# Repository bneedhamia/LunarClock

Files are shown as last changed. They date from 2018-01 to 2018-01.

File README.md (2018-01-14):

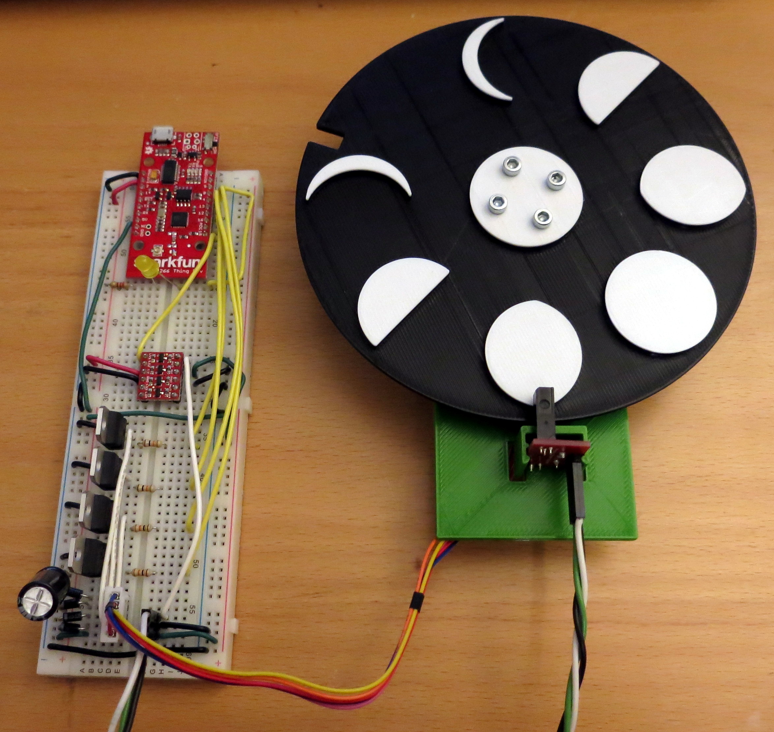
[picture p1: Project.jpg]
The Project so far

# LunarClock
An ESP8266 Thing Arduino Sketch to display the current phase of the moon,
as reported by
[HM Nautical Almanac Office: Miscellanea, Daily Rise/set and Twilight times for the British Isles](http://astro.ukho.gov.uk/nao/miscellanea/birs2.html). It does this by rotating a disk
that has 8 lunar images on it, to align the appropriate image with a window in the clock.

That page provides the time of sunrise/sunset/etc., for many locations in Britain and Ireland.
The end of that page provides the age of the moon (days since the new moon) and
the percentage of its face that is illuminated. Of all that information, only the age of the moon
is used by this Sketch.

The current Sketch requires a Sparkfun EPS8266 Thing Dev board, a Photo-interrupter,
and an AdaFruit 28BYJ-48 12V stepper motor, among other things.
Details are in the .ino Sketch PIN_ definitions and in BillOfMaterials.ods.

NOTE: This is a work in progress.

State of the project: On reset, the Sketch turns the lunar disk wheel to find the slot, then turns it to align
the first lunar image in the (to be built) clock window. It then connects to the local WiFi,
reads and parses HM Almanac page mentioned above, and rotates the wheel to show the corresponding
lunar image. It then stops. Further major changes await the design of the clock face and box.

Next steps: design the 3D printed clock face and box;
finish writing the state machine code, to retry wifi failures and query the site once every day.

## Files
* BillOfMaterials.ods = the parts list
* LICENSE = the project GPL2 license file
* LunarClock.ino = the ESP8266 Thing Dev board Arduino Sketch
* LunarClockDiary.odt = my project diary.  All of the little details of the path from idea to reality (so far)
* lunarDisk.FCStd = FreeCAD model file for the 3D printed lunar images disk and holder for stepper motor and photo interupter.
* LunarDisk.stl = 3D printable file of the disk of lunar images. Swap filament in mid-print to print light lunar images on a dark disk.
* LunarWheel.svg = (obsolete) Inkscape (laser cutting) file for the wheel of lunar images.
* Project.jpg = a photo of the project so far
* README.md = this file
* StepperHolder.stl = 3D Printable file for the plate that holds the stepper motor and photo interrupter.
* XXXXX to add as I create them: fritzing diagram; mechanical and assembly notes; other files for 3D printing.

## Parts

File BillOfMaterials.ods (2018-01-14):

Bill Of Materials for ESP8266-Controlled Lunar Clock
Count | Name | Supplier | Part Number | Cost each | Total | Url | Notes
1 | SparkFun ESP8266 Thing - Dev Board (with Headers) | Sparkfun | WRL-13804 | $16.50 | $16.50 | https://www.sparkfun.com/products/13804 | ESP8266 Thing is a 3.3V WiFi processor programmable via the Arduino IDE.
1 | Wall Adapter Power Supply - 5.1V DC 2.5A (USB Micro-B) | Sparkfun | TOL-13831 | $7.95 | $7.95 | https://www.sparkfun.com/products/13831 | This supply powers both the ESP8266 and the stepper motor
1 | 28BYJ-48 12V unipolar stepper motor, 5mm flattened shaft | Adafruit | 28BYJ-48 12V | $4.95 | $4.95 | http://www.adafruit.com/products/918 | To rotate the wheel of lunar images. Note: other motors with the same part number and voltage have different specifications (steps per revolution, resistance). Double check the specs before buying.
1 | Actobotics Set Screw Hub - 5mm Bore | Sparkfun | ROB-12404 | $4.99 | $4.99 | https://www.sparkfun.com/products/12404 | 5mm and set-screw to fit the stepper shaft and hold the lunar images disk.
1 | Machine Screw - Socket Head (6-32 ; 1/2"; 25 pack) | Sparkfun | ROB-12415 | $2.95 | $2.95 | https://www.sparkfun.com/products/12415 | to hold lunar disks wheel to hub. We need only 4, but they come in a set of 25
1 | Photo-interrupter, 10mm gap | Sparkfun | SEN-09299 | $1.95 | $1.95 | https://www.sparkfun.com/products/9299 | The lunar images disk slot is designed to fit this part.
1 | Photo-interrupter breakout board | Sparkfun | BOB-09322 | $1.50 | $1.50 | https://www.sparkfun.com/products/9322 | The 3D printed clip is designed to hold this board.
1 | SparkFun Logic Level Converter – Bi-Directional | Sparkfun | BOB-12009 | $2.95 | $2.95 | https://www.sparkfun.com/products/12009 | For shifting the 5V Photo-Interrupter output to 3.3V for ESP8266 input.
1 | Resistor, 220ohm, 1/4watt, 5% |  |  | $0.00 | $0.00 |  | Current limit resistor for the LED
1 | Breadboard - Full-Size (Bare) | Sparkfun | PRT-12615 | $5.95 | $5.95 | https://www.sparkfun.com/products/12615 | XXX Rethink how to distribute Vin vs. 5V. I might use 2 half-size breadboards to fit in the clock box better.
1 | Hookup wire, solid, 22Awg, white | Sparkfun | PRT-08026 | $2.50 | $2.50 | https://www.sparkfun.com/products/8026 | Signal wires
1 | Hookup wire, solid, 22Awg, black | Sparkfun | PRT-08022 | $2.50 | $2.50 | https://www.sparkfun.com/products/8022 | Ground wires
1 | Hookup wire, solid, 22Awg, red | Sparkfun | PRT-08023 | $2.50 | $2.50 | https://www.sparkfun.com/products/8023 | 3.3V Power wires
1 | Hookup wire, solid, 22Awg, yellow | Sparkfun | PRT-08024 | $2.50 | $2.50 | https://www.sparkfun.com/products/8024 | Arduino signal wires
1 | Hookup wire, solid, 22Awg, brown | Sparkfun | PRT-08027 | $2.50 | $2.50 | https://www.sparkfun.com/products/8027 | Vin wires. Normally I use Green
1 | Break-away headers – straight, 40 pins | Sparkfun | PRT-00116 | $1.50 | $1.50 | https://www.sparkfun.com/products/116 | 5 pins for the stepper motor connections; 3 for the photo-interrupter
10 | Diode, 1N4004, 400V, axial, Cut Tape | Digikey | 1N4004FSCT-ND | $0.17 | $1.67 |  | Need 4 for the stepper. They come in lots of 10.
4 | Transistor, TIP120, TO-220 | Digikey | 497-2539-5-ND | $0.56 | $2.24 |  | For steppper control
4 | Resistor, 1Kohm, 1/4 watt, 5% |  |  |  |  |  | For steppper control XXX tally up when you count parts.
1 | Capacitor, 1000uF, 25V, radial | Digikey | 493-5913-1-ND | $0.51 | $0.51 |  | To smooth the mA demand of the stepper motor. Buy at least 10 because you'll need them for other projects.
65 | Approximate grams of filament for 3D printed parts |  |  | $0.03 | $1.63 |  | Use whatever filament you like. I used black for the lunar disk and white for the lunar images. I used $25/Kg filament.
0 | XXX more to come: Molex connectors, etc. |  |  | $0.00 | $0.00
Grand Total |  |  |  |  | $69.74
Tools
1 | Lulzbot Mini 3D Printer | Lulzbot | Mini | $1,250.00 | $1,250.00 | https://www.lulzbot.com/store/printers/lulzbot-mini | To print the 3D printed parts. TO DO add the printer requirements: print size

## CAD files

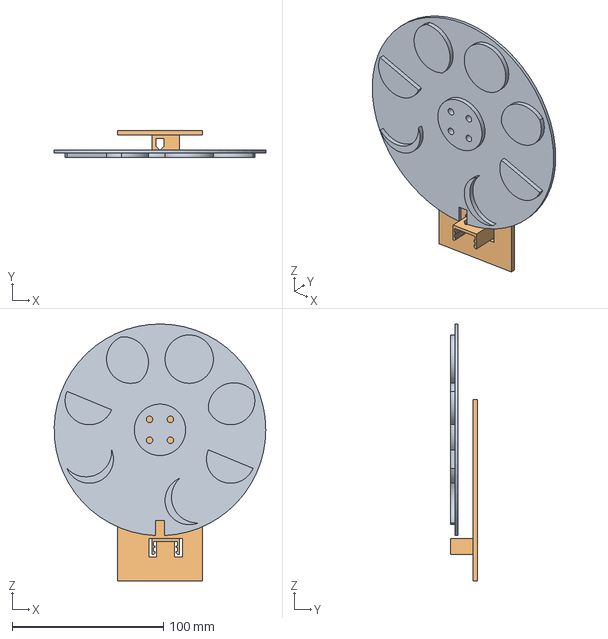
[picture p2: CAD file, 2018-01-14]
lunarDisk.FCStd
140.0 x 18.0 x 170.0 mm
partDiskPlusImagesComplete
partStepperOptoHolderComplete

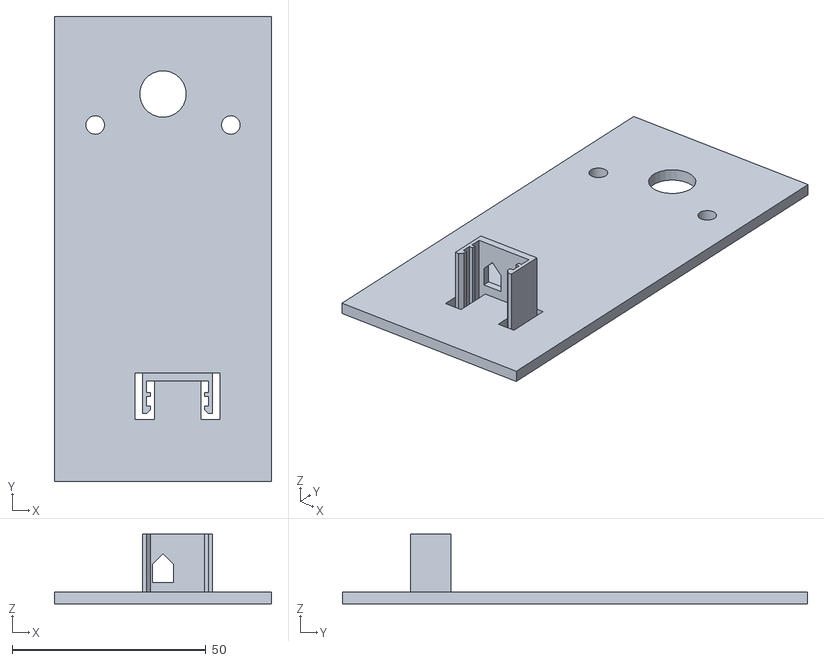
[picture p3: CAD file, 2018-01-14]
StepperHolder.stl
56.0 x 120.0 x 18.0

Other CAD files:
LunarDisk.stl

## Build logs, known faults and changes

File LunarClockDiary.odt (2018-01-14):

Lunar Clock Project Diary

Every project should have a project diary, to record all the little bits of info and the wrong turns I find along the way toward the final project.

# Summary

The idea is to have a cabin-kitsch (in a good way) box that sits on the mantel and shows the approximate phase of the moon. Try acrylic paints to give that craft look.

I'm planning on a wheel of images of the moon in various phases, which rotates behind a set of clouds. The center of the clouds contains a round hole the size of one of the lunar images. The rest of the scene may include a dog baying at the moon, a hill, and a cabin.

I'm currently planning for the wheel to contain 8 images of the moon's phase, from new moon to full moon and back to nearly new. One lunation (new moon to new moon) is about 29.53 days long, so with 8 images the image should change about every 3.7 days. I'd like it to change more often than that, but I'm concerned that a wheel of 12 or more images would be too large (a small moon in a large wheel).

About once every 3 or 4 days the wheel turns to reveal a new image of the moon. http://stardate.org/nightsky/moon gives a calendar of the moon, which is useful for deciding how many phases the design will support.

The only reasonably-public phase of the moon site I've found so far is: HM Nautical Almanac Office: Miscellanea: Daily Rise/set and Twilight times for the British Isles, at

http://astro.ukho.gov.uk/nao/miscellanea/birs2.html. I've found many sites that give the percent of the moon that's illuminated, but that don't distinguish between waxing (moving toward the full moon) and waning (moving toward the new moon).

An alternative to reading the lunar phase would be to calculate it. Without a full calculation, you can do a simple calculation from the time of a recent full moon (29.530… days per lunation). But since we need to use a web site to get the current date and time, we might as well read the phase as well.

Be sure to specify HTTP 1.0 in the request rather than HTTP 1.1. HTTP 1.0 prevents the server from using Transfer-encoding: chunked, which is difficult to decode by hand.

http://playground.arduino.cc//Code/Webclient is an example of getting the date and time from a web server's response.

http://aa.usno.navy.mil/faq/docs/moon_phases.php has a good list of named images of the phases of the moon.

# Next Steps

- Design the front of the clock. That is, draw what the picture will be the face of the clock: the moon, and possibly clounds, a dog, a house, and stars.
- Rotate the images of the moon on the disk so that when each image is rotate into place, it’s oriented properly with respect to the clock face.
- Decide how the stepper and opto-interruper holder will fasten into the larger clock box.
- Decide how to print the large clock box exterior parts on the 150 mm cube Lulzbot Mini.
- Design the 3D printed lunar clock box.
- Add the Wait state so the Sketch will periodically query the web site rather than doing it only once. Consider short waits for connection failures; very long waits (a day) for waiting til it’s time to query again. But avoid choosing wait times that are so short as to look like (or be) a denial of service.
- Finish porting the HTTP code:
  - See if there’s a way to set the security type and timeout for connecting to the WiFi router.
  - See if there’s a way to read the HTTP Get response header in the ESP8266 library.

# Diary

## Saturday January 13, 2018 – Adjusting the Opto-interrupter holder

I found the hub of the stepper motor isn’t exactly perpendicular to the stepper motor holder, which makes the lunar disk move forward and backward a bit (1 or 2 mm) as it rotates. I raised the opto-interrupter a little bit to make sure it has enough clearance for the slightly off-flat lunar disk.

Later in the day I discovered the stepper motor axis is off because the whole stepper motor is at an angle. This is because the hole for the motor axle isn’t big enough. I increased the size of the hole and now the disk is nicely flat with respect to the motor holder plate.

The opto-interrupter pushes into the clip really easily. It’s very hard to get the opto-interrupter out of the clip, but that’s ok, because I’ll be taking the clip out on rare occasions.

## Friday January 12, 2018 – Opto-interrupter holder design

Did a couple experiments of 3D printed clips to hold the opto-interrupter in place. Settled on a pair of side clips that are quite tight, but seem to work fine. Added that clip design to the plate that holds the stepper motor. Once a test print works, I’ll be back where I was in September, but with a 3D printed design.

## Wednesday January 10, 2018 – Opto-interrupter holder design

Tweaking the bars of the opto-interrupter clip so they fit around the parts on the opto-interrupter’s breakout board. Next step: the clip that will hold the board in place.

## Sunday January 6, 2018 – Opto-iInterrupter holder design

Working out a 3D printed holder for the Opto Interrupter. I’ve tried a couple approaches to it. I’m currently working toward a design that the Opto Interrupter will clip into, without screws, nuts, etc.

## Saturday December 9, 2017 – more lunar wheel design

Working out the angles to rotate the moon images to so that the image at the top of the disk is upright – just as a test.

Here’s a list of amount to rotate each lunar image clockwise (negative degrees in FreeCAD) from its upright orientation. The index 0 corresponds to the full moon. Index 1 = the moon Counterclockwise from the full moon (the waning gibbous moon). Thinking about this, I see I should probably simplify angles and names by putting the new moon at the top, but not yet.

After wrestling with incorrect angles for quite a while I remembered that I had rotated opposites rather than mirroring them (which has its own problems). I forgot to take that rotation into account. What a mess. Decided to start all over with the lunar images, making each one independent rather than a mirror or rotation of some other. I’d need to do this if the lunar images showed the moon itself, because for example a waxing crescent lights a different part of the moon than the waning crescent.

In recreating the partial moons (e.g., waxing crescent) I realized I’d forgotten to document why I chose the 45° angle of the circle for the partial moons rather than the half way point between the lunar image edge and center. The answer: I wanted each lunar image to be an equal number of days apart. That is, the images as I’ve defined them break the 29.5 day synodic month (full moon to full moon) into 8 pieces, each piece being about 3.69 days from the previous one (29.5 / 8 = 3.6875).

(re)created all the images of the moon. I used the imagePositioningGuide Sketch to line them up on the disk: full moon just to the right of the top, and waning gibbous, etc. counterclockwise from there.

Index, angle, where angle = 22.5 - 45 * index

0 22.5 Full Moon

1 -22.5 Waning Gibbous

2 -67.5 Last Quarter

3 -112.5 Waning Crescent

4 -157.5 New Moon (blank)

5 -202.5 Waxing Crescent

6 -247.5 First Quarter

7 -292.5 Waxing Gibbous.

Resigned the opto-interrupter holder to be a block with a slot cut in it. Still in progress.

## Friday December 8, 2017 – lunar wheel 3D print design

Designed simple slices for the phases of the moon (the new moon is black), where the lighted part is raised above the bed. The idea is that I’ll print it in black or dark blue, then switch to yellow when it starts printing the moon images.

Noticed the disk needs a thicker center, to keep the hub screws from scraping the stepper motor holder. The disk needs to be 5mm thick at the hub screws. Also, because the outer face of the hub is already in the middle of the opto-interrupter slot, I should thicken the outer face of the lunar disk rather than the inner face (thickening the inner face would raise the outer disk surface, by the way it would also be hard to print without support).

## Thursday December 7, 2017 – 3D clip for photointerrupter

Designing a 3D printed thing to hold the photo-interrupter (disk slot detector).

## Tuesday December 5, 2017- more 3D printing design

I’m using a 28BYJ-48 12V stepper motor. I found a plausible mechanical datasheet for it, at https://tutorials-raspberrypi.de/wp-content/uploads/2014/08/Stepper-Motor-28BJY-48-Datasheet.pdf It gives the centers of the two screw holes as 35 +/-0.1mm apart, with a diameter of 4.2+/-0.1mm. Further, the motor shaft is centered horizontally between the two screw holes, and is 8+/-0.1mm above them (when facing the shaft). The non-moving outer collar of the shaft doesn’t seem to be given; I measured it at 9.09mm diameter.

## Sunday December 3, 2017 – messing about with 3D printed disk

Just for grins, I’m looking into what the lunar disk would be like if I printed it on my Lulzbot Mini (152mm square bed). I chose a lunar disk radius of 70 mm radius (140 mm diameter).

Looking for specs on the hub holes, I found the Sparkfun product page points to https://www.servocity.com/770-set-screw-hubs, which says the holes are 6-32 UNC holes. Then I found https://www.design1st.com/Design-Resource-Library/engineering_data/TapDrillClearanceHoles.pdf, which gives the normal clearance for a 6-32 screw as 4.32mm diameter. The product page says the holes are 0.770 inches (or 19.558 mm) apart at the diagonal of the square layout of holes. Converting that to the horizontal or vertical distance between the holes: 0.770 / sqrt(2) = 0.5444 inches, or 13.827mm. Half of that gives the distance from horizontal or vertical center to the center of the hole: 6.9148mm. Let’s try 6.9mm.

For a 70mm radius disk, the largest possible lunar images would be 19.37mm radius each. To allow a gap between disks so that a hidden disk won’t show an edge, I chose about 6mm between disks. So I chose a lunar image radius of 16mm (19.37 – 6/2 = 16.37mm, then I rounded down).

Looking for public domain images of the full moon, I found https://www.metmuseum.org/art/collection/search/393543 (Metropolitain Museum of Art). Found a nice image from wikipedia, with an attribution and share alike license: attribution is “By Gregory H. Revera - Own work, CC BY-SA 3.0, https://commons.wikimedia.org/w/index.php?curid=11901243”, which includes the url.

Test printed a lithophane of that moon. 2 (3?) mm high, heavy smoothing. Also test printed the hub holes. The lithophane didn’t turn out well (too thin); the test hub fit perfectly. Did a test print of the full-sized lunar disk.

## Tuesday September 5, 2017 – Net seems to work

I read a few examples and comments about the ESP8266 Arduino library, and decided to add some configuration to the setup(): 1) Explicitly putting the WiFi in Station (client) mode – it’s possible the default is dual, that is client plus a soft access point

Tried out the new state machine code for finding the disk slot; code that does only one step() per loop() rather than executing one loop() that takes seconds to finish. That seems to work great, but the net didn’t connect.

I then added two more explicit WiFi settings in setup(): 1) turn off autoconnect – some users complain that by default the lib tries to connect using the last-used parameters, 2) explicitly turned on reconnect() - seemed like a good idea to reconnect automatically if the connection drops. Although now that I think about it, I’m not sure I want this device to be continuously connected to the AP. ...although it sounds like continuous connection is the model the ESP8266 lib developers used.

With the added calls, the WiFi part seems to work! On reboot the disk rotates to the slot, then rotates to the first lunar image, then successfully connects to the net (after a little while, but not an unreasonable time). Score!

Updated the Bill of Materials to reflect the ESP8266 design. Did a pass through the ReadMe.md etc. Added a photo of the project so far.

By the way, swapping the Arduino Mega, CC3300 Shield, and Transmogrishield for an ESP8266 Thing Dev board saves about $80 on this about $180 project.

Modified the State Machine to step() only once per loop() to turn to a lunar image. Moved the connection to the AP to setup() with the assumption that the ESP8266 will keep us connected (if possible) from there on. Did a little more cleanup.

## Monday September 4, 2017 – Rewriting the state machine

On a hunch, I added a 1000 microFarad capacitor between the stepper motor’s power and ground. It’s probably useful, but it didn’t fix the inability to connect to the WiFi router.

Realised I’m changing way too many things at once, so decided to back up and 1) clean up the code layout and variable names without changing the logic then 2) rewrite the state machine to make rotating the disk by one step part of the state machine.

Did a commit of just name/order changes (no semantic changes).

Modified the state machine; haven’t tested that code yet.

## September 3, 2017 – Wiring the Stepper motor, photo-interrupter, and fixing wifi again

I transferred the stepper motor transistor circuit from the Mega breadboard to the ESP8266 breadboard, updated the pin numbers in the Sketch, wired the common stepper pin to 5V (V_USB) on the ESP8266, and changed the Sketch state machine to start at rotating the disk. It worked the first time!

Note: the current calculations above show that the stepper motor will be pulling about 124mA on a 50% duty cycle while the disk is turning. The ESP8266 Thing Dev schematic suggests the V_USB is the nominal 5V directly from the USB connector, so I think a USB supply should be able to supply the 124mA we need.

Dug through my Sparkfun boxes to find the level shifter I bought from Sparkfun a while ago. I need it to shift the photo-interrupter output from 5V to 3.3V. I soldered the header pins onto the level shifter.

Wired up the level shifter. When I turned on the ESP8266, it just kept resetting, which suggests that the circuit is miswired. Disconnected the level shifter output from pin 2 and it worked fine (but of course can’t sense the photo-interrupter). After a bit of probing with a voltmeter to see that voltages on both sides of the level shifter looked good, I noticed that the 5V power supply reads 4.87V while the stepper motor is running and 4.96V when it isn’t. That difference tells me that the power supply isn’t capable of driving the stepper motor :-( Measured the current draw of the motor while it’s running: average 72mA, which is what I expected: ~124mA at 50% duty cycle = ~62mA.

On a whim, connected the photo-interrupter output directly to pin 2 (photo interrupter input). It caused continuous resets (on reflection, that was a really bad idea, to connect a 5V output to an ESP8266 3.3V input). Suspecting something magic about pin 2, I changed the code to use pin 15 for the photo-interrupter, wired pin 15 to the ouput of the level shifter, and the slot detection now works.

Unfortunately, after the stepper motor rotates to the first moon image position and the Sketch starts trying to connect to the WiFi router, it shows the same problem it had before I removed the long delay() calls: it just waits and waits and never connects.

To test that the web query still works, I changed the code back to start with the web query rather than the disk rotation. The Sketch successfully connected to the router, but failed to get the web page. Manually attempting to read that page via Chrome returned a timeout – I wonder whether the site is just temporarily down (it’s Sunday of a Bank Holiday in the UK) or whether the site has decided my IP address has been making too many queries, and blocked my IP. I’ll assume the first and try again later.

At any rate, the experiment showed the connection to the router succeeds if it’s done first, and fails if it’s attempted after running the stepper motor.

Messing with the delays in the find-the-slot code, I found that if the Sketch rotates the disk only a little, the wifi connection works; if it rotates it a lot, the wifi connection fails. I wonder whether the loop simply can’t take a long time, regardless of whether delay() is called within that long delay.

Started rewriting the wheel movement code to make “move the wheel a step” be part of the state machine.

## September 2, 2017 – Getting Arduino to compile ESP8266 Sketches again

Plugged in an ESP8266 Thing Dev board into my Windows machine and started Arduino IDE… it doesn’t have the ESP8266 support installed. The weird thing is that I could swear that around July I had tried out the ESP8266 Thing, Red Bear BLE, and one or two other unusual Sparkfun IoT boards. Perhaps I removed the support for them when I was done? That rings a bell.

At any rate, I reconciled my github repo copy of LunarClock and reinstalled the ESP8266 Arduino support, selected Sparkfun EXP8266 Thing Dev board, plugged in my board and compiled the LunarClock Sketch (with errors).

My main concern now: does the ESP8266 Thing Dev board have the Ram and Flash necessary to run the Lunar Clock Sketch? I imagine it has enough because it’s designed to do the sort of thing I’m doing: talk to a web site and control a few things.

Back to the compile errors: the error text gave no insight into the problem, so I decided to compile and run Blink first. Blink didn’t compile either. Hmm. Tried compiling for Arduino Uno and Blink. Compiled fine. Uninstalled and reinstalled the ESP8266 board support; blink still didn’t compile. The error is nothing more than

Arduino: 1.8.4 (Windows 10), Board: "SparkFun ESP8266 Thing Dev, 80 MHz, 115200"

…

"C:\Users\Brad\AppData\Local\Temp\arduino_build_934615\preproc\ctags_target_for_gcc_minus_e.cpp"

exit status -1073741515

Error compiling for board SparkFun ESP8266 Thing Dev.

I’m beginning to suspect I messed up my Arduino installation by uninstalling the ESP8266 support a few months back. Some Windows components don’t like things being uninstalled an reinstalled (they are Bad Code, of course). My next course is to uninstall Arduino IDE and reinstall it. It doesn’t help that Windows 10 Software Store hides almost all details of the installation.

Googling a bit shows that the error I’m getting seems to be associated with “can’t find a component”. So I’m going through the prerequisites of ESP8266 development, at http://esp8266.github.io/Arduino/versions/2.3.0/doc/installing.html. The prerequisites are:

- Arduino 1.6.8 (or newer, if you know what you are doing)
  - This one is a bit of a puzzle, because different Arduino platforms seem to have different basic version numbers. My Windows 10 Arduino IDE reports its version as 1.8.4.
- (installed) git
- (installed. I have python v2.7.12) python 2.7
- (comes with Windows) terminal, console, or command prompt (depending on you OS)
- (Yes) Internet connection

Since I have the prerequisites, I guess I do need to uninstall and reinstall the Arduino IDE. Bummer, dude. By the way, searching for “esp8266” on my C: drive turns up no less than 6 copies of what looks like ESP8266 support. Tip to developers: if your app has a cache, provide a way to clear it.

Using the Arduino IDE board manager, I uninstalled ESP8266 support, then I searched for “esp8266” in the file explorer again. It still turns up over 5 copies of esp8266, under AppData/Arduino and Documents/ArduinoData.

In preparing to uninstall Arduino IDE, I took the opportunity to clear out a lot of obsolete Sketches I’ve written over the past few years.

Moved my Sketches and libraries to a backup folder, uninstalled Arduino, manually deleted the Arduino folder, the ArduinoData folder, AppData/…/Arduino15 folder. Verified that all esp8266 folders were gone, via search in File Explorer for “esp8266”. Rebooted, downloaded Arduino 1.8.4 (rather than installing from Windows Store), moved back my Sketches and libraries. Checked that Arduino compiles Blink for Uno. Installed ESP8266 2.3.0 support from Sparkfun instructions (actually, community instructions at https://github.com/esp8266/Arduino#installing-with-boards-manager).

SUCCESS! Blink compiled fine for Sparkfun ESP8266 Thing Dev board.

### Porting LunarClock to ESP8266

Compiled LunarClock for Sparkfun ESP8266 Thing Dev board. Of course, it doesn’t like the CC3300 library inclusion. Tried to do some quick hacks to get LunarClock to compile, but after a lot of slogging through compile errors, decided there’s too much to rewrite.

I wrote a simple echo Http Get client for ESP8266, and it (eventually) worked. Folded those changes into LunarClock, and they don’t connect. Hmmm.

Modified write_eeprom_strings to work for ESP8266, and to remove the obsolete .length() call. Folded those changes into Lunar Clock.

Current state: Lunar Clock successfully reads the Wifi SSID and password, but doesn’t seem to connect. Need to add code to detect failures other than ‘not yet connected’.

After MUCH experimentation, I found the connection problem was the Lunar Clock large delay() calls. I had seen a note in the ESP8266 library documentation that said to avoid long periods when the WiFi could not run in the background. I hadn’t realized that delay(5000) gives the WiFi only one chance to run in a 5 second period of time – which is too long.

Fixing that, the next problem was that the ESP8266 Http library doesn’t return headers via the main stream. I temporarily commented out the date reading code, and the Web interface code now properly reads the age and illumination of the moon again!

## September 1, 2017 – considering replacing the Arduino; reviving the project.

Sparkfun has discontinued the Transmogrishield. Also, an Arduino Mega seems way overkill for what I want to do. In the meantime, I’ve had good success playing with a Sparkfun ESP8266 Thing dev board, which looks like a promising replacement.

Since the ESP8266 is a 3.3V part rather than a 5V part, I need to check and/or adapt the I/O circuits to work with 3.3V instead of 5V. Good news: the TIP120 seems to happily turn on at 2.5V, so using a 3.3V Arduino output should work fine.

Bad news: the Photo-Interruptor I’m using is clearly a 5V part: the datasheet says Vcc must be 4.5V to 17V, and the sensor output High level has a minimum of 4.9V.

Mixed news: the ESP8266 power supply must be no higher than 6V, so I can’t power it with a nominally 9V Arduino supply and use that 9V to drive the stepper motor. So it looks like I should try powering the ESP8266 from a USB charger, and use the (5V I assume) VIn pin to drive the stepper motor, the photo-interrupter, and a 3.3V-5V level shifter. If Vin isn’t regulated well enough, I can add a 5V regulator; I have bunches of those left over from my PIC development days.

Since I’m now very comfortable with design for 3D printing, I should reexamine what parts of the project can be 3D printed.

Good news: I plugged in the stepper motor and photo-interruptor, plugged a USB cable into the Mega, and the circuit worked. I’m used to projects sort of falling apart if you leave them alone for over a year, but this one seems to be working.

I measured the voltage to the stepper motor, and it was 4.3V (I’d expect 5V from a USB cable, but 4.3V is ok). The stepper seems to have enough energy to move the lunar imges disk. It’s easy to stop it with a finger, but I think it will work fine with 5V.

### January 1, 2016 – Wired and mounted the photo-interrupter

I tried the Molex crimp connectors on 22 gauge stranded (vs. solid) wire. After a few false starts the crimping worked fine. I then realized the reason I was having such trouble with the cat3 wire: the crimper has a wide side (for the insulated wire) and a narrow side (for the connector). When I was trying to crimp onto the cat3, I was probably putting the connector in backwards, which made the insulation crimp far too tightly, breaking the wire.

At any rate, the stranded wire will be more flexible than solid wire would, so that's a good step.

I wrote a blog entry today about how I modified an angle bracket (“corner bracket”) to mount the photo-interrupter. I hacksawed one end of the bracket to make it low enough, then drilled three mounting holes: one to connect to the mdf connected to the photo-interrupter breakout board, and two to connect to the strip of mdf that holds the stepper motor. It worked great.

With that mounting in place, I temporarily adjusted some constants so that the proper lunar image appears opposite the photo-interrupter.

### December 31, 2015 – bought paints

Today I bought a starter set ofAcrylic paints (similar to http://www.amazon.com/Art-Advantage-4-Ounce-Acrylic-Primary/dp/B0025TZ05O) and brushes (http://www.amazon.com/Connoisseur-Fine-Art-Products-Protege/dp/B00HNKTK06) from a local artists' supply. Acrylic paints are non-toxic, and - while wet - wash out with water.

## November 22, 2015 – failed at wiring the photo-interrupter; sealed the lunar disk

For some reason I'm having a terrible time attaching simple Molex crimp connectors to some old Cat 3 telephone cable. I intend the cable to connect the photo-interrupter to the breadboard. I tried several times and for some reason the wires kept breaking at the point they attach to the crimp connector – I'm not sure what's wrong. I'm a bit stumped. Maybe the wire is so old it's become brittle – it is after all solid wire rather than stranded.

Today I sprayed the lunar disk with Krylon Crystal Clear Acrylic Coating 1303A (http://www.amazon.com/Krylon-1303-Acrylic-Crystal-11-Ounce/dp/B00023JE7K), to seal the disk so I can paint the lunar images onto it.

I've been a bit distracted by the Build Your Own CNC Machine project, as I put off designing the front of the lunar clock, which is artistically the complex part.

## November 3, 2015 – Checking resistance variation in steppers

A friend of mine at work recently bought a set of 28BYJ-48 5V stepper motors, from a source different from AdaFruit. Based on the variation in datasheets I'd seen, I wanted to see if the resistance of these motors were different from the 5V motor I'd bought from AdaFruit.

28BYJ-48 5V #1 | Blue | Pink | Yellow | Orange | Red
Blue | - | 51.7 ohm | 51.8 | 51.4 | 26.0
Pink | | - | 51.8 | 51.4 | 26.0
Yellow | | | - | 51.5 | 26.1
Orange | | | | - | 25.7
Red | | | | | -

Pretty close to the 50-51ohm and 25ohm I'd measured in my motor.

28BYJ-48 5V #2 | Blue | Pink | Yellow | Orange | Red
Blue | - | 51.5 ohm | 51.2 | 51.5 | 25.7
Pink | | - | 51.6 | 51.9 | 26.0
Yellow | | | - | 51.7 | 25.8
Orange | | | | - | 26.1
Red | | | | | -

28BYJ-48 5V #3 | Blue | Pink | Yellow | Orange | Red
Blue | - | 51.3 ohm | 51.2 | 51.0 | 25.7
Pink | | - | 51.4 | 51.1 | 25.8
Yellow | | | - | 51.1 | 25.8
Orange | | | | - | 25.5
Red | | | | | -

So those motors from another source seem pretty much the same as the one I bought from AdaFruit, which is good.

Meanwhile, I read a little about MDF and Acrylic paint. It turns out artists who work in acrylic often paint on MDF, and strongly recommend a sealer to prevent the paint from absorbing into the MDF and causing it to swell. I think I'll try Krylon clear acrylic coating aerosol spray paint on the lunar disk.

I soldered the photo-interrupter parts to the Sparkfun breakout board that I'd drilled two holes in, and tested it: it seems fine.

## November 1, 2015 – checking the stepper play

I tried leaving 1 pin energized rather than shutting off all stepper pins when the wheel stops. It didn't seem to make much difference. I tried the Stepper library, which leaves 2 pins active. It didn't seem to make much difference.

So it looks like this motor has a few degrees of play that I have to allow for. Seems odd in that positional accuracy is sort of what you want a stepper motor for.

Meanwhile I took a quick look at a few gearhead motors. The big disadvantage of those is that their stall current can be large (like 500mA to a couple Amps), and they're more expensive (midrange is about $12-$18).

Turning to the mechanical design: the stepper motor mounting seems easy; the photo-interrupter is giving me fits because it has the breakout board has no mounting holes. Examining the board, there seemed to be room to drill two mounting holes, and it seemed to be a two-sided board with a ground plane. So I drilled two mounting holes through what seemed like empty space on the board. Checking with a multimeter, the mounting screw is connected to ground, but the holes don't seem to have done any damage. It's a hack, but it seems to work.

## October 31, 2015 – Lunar disk arrived from Ponoko

The laser cut lunar disk I ordered on October 24 from Ponoko arrived today! The four screw holes for the setscrew hub, and the photo-interrupter slot were perfect, as was the engraving of the guides for painting the lunar disks. It would have taken a huge amount of work for me to cut those so accurately on my scrollsaw.

One small down side: the laser cutting burns the wood (duh), causing a smell that to me seemed like codfish oil – very unpleasantly fishy. After airing out the parts for a few hours that smell was negligible.

Once I fastened the disk securely to the stepper motor I found that there is a lot of play (a few degrees) in the motor angle when the motor is not energized – once the wheel stops, the lunar disk could be a few degrees one way or the other from where I want it. So I need to write a little stepper library example to see what the play is when the motor is energized. I'd rather not keep the motor energized because that would burn about 224mA continuously, which is a lot for a wall clock to consume.

With the uncertainty of the wheel placement (the play), I'm wondering whether this would work better with a gearhead DC motor and a slot for each lunar disk, rather than an accurate stepper motor with a less accurate unenergized position. That would require precise placement of the photo-interrupter, but would likely (with a high gear ratio) have a lot less play.

P.S., about doing the parts cutting myself: I've finished reading “Build your own CNC Machine”, by Patrick Hood-Daniel and James Floyd Kelly: http://www.amazon.com/Build-Your-Machine-Technology-Action/dp/1430224894. It sounds plausible that I could build one with little trouble and a lot of labor, resulting in something that could cut up to 2-foot by 4-foot pieces of wood and plastic. I'm still unclear on what CNC Open Source software to use, and what stepper motor control to use (e.g., an Arduino PC peripheral vs. a standalone Raspberry Pi or Edison).

## October 29, 2015 – Removed the Stepper library

Replaced the use of the Stepper library with my own code, so the motor would have more torque (by half-stepping) and be turned off when not in use – I expect the motor's unenergized torque will be enough to hold the wheel in place.

Experimented a bit with the motor, double-checking steps per revolution and range of RPM. Looks like the stepper motor work is completed!

### October 28, 2015 – Integrating the 12V motor

I need to find the steps per revolution. The emartee datasheet above gives a stride (step) angle of 5.625 degrees / 64 (it has a 1/64 gear ratio). So the steps per revolution is 360 / (5.625 / 64) = 4096.

Using stepper(4096, pin...) and calling step(1) 4096 times produced about... 8 and ¼ revolutions.

Meanwhile, the Adafruit page for this stepper (http://www.adafruit.com/products/918) says it has 32 steps per revolution (not degrees per step) with a 1/16.025 gear ratio. That gives 32 * 16.025 = 512.8 steps per revolution. Rounding to 513 minimizes the error.

Using stepper(513, pin...) produced... something that looks a lot like one revolution.

So for inexpensive parts like these stepper motors, just because a part has the same part number doesn't mean it has the same specifications.

Note: because the true steps per revolution is 512.8 and we're rounding up to 513, using integer steps per revolution would have an error of 513 – 512.8 = 0.2 steps per revolution. That's an error of (360 / 512.8) * 0.2 = 0.14 degrees per revolution. Let's assume that the wheel would have to be 3 degrees off for the lunar image to not align well (we can measure what it really is once the clock is complete). So it would take 3 / 0.14 = about 21 revolutions to have a problem. Since our clock runs one revolution per month, that would take about 21 months, or 21 / 12 = very roughly two years running continuously without a reset to cause a problem. Since our house power goes out briefly several times per year (which would reset the wall-powered clock), this error doesn't look like it would be significant.

I won't test RPMs because I'm going to use ms per step instead. But I will say that at 48 rpm and no load the motor ran nice and smoothly, and below about 15 rpm it had an audible rattle.

### October 27, 2015 – The 5V motor

Looking at the Adafruit 28BYJ-48 5V version.

28BYJ-48 5V | Blue | Pink | Yellow | Orange | Red
Blue | - | 50 ohm | 50 | 51 | 25
Pink | | - | 50 | 51 | 25
Yellow | | | - | 50 | 25
Orange | | | | - | 25
Red | | | | | -

Once again, the Red pin is the common.

Current: It's rated at 5V, so 5/25 = 0.200A or 200mA. Since the stepper library runs two pins at once all the time, the current will be 2 * 200mA, or 400mA. That's way too much for an Arduino, so this motor is consigned to the parts cabinet to await another project.

Turning back to the 12V motor, I'm having a lot of trouble finding a datasheet for it. Lots of places offer that part number motor in 12V, but the datasheets vary a lot – one even shows the 5 wires in the mechanical diagram, but shows only 4 in the electrical diagram. One seems reasonable: http://www.emartee.com/product/41757/, but it lists the resistance as 200ohms +/-7%, which is a long way from 160ohms. That suggests that I should re-measure the resistance of each motor I use.

I'm leaning away from using the Arduino Stepper library because 1) it doesn't do half steps, and half steps on my old motor produced much higher torque 2) it leaves the motor energized at the end, meaning that my circuit would be burning 124mA constantly to keep the wheel from turning. The unenergized motor seems to have enough torque to prevent the balanced lunar wheel from slipping.

### October 26, 2015 – Checking out the Adafruit stepper motors.

The two Adafruit stepper motors arrived today. One is a 12V motor; the other is a 5V motor.

The manufacturer's datasheet for the 12V motor is at http://www.sensors.co.nz/datasheet/28BYJ-48%20Stepper%20Motor.pdf (oops – that's the 5V datasheet. I can't seem to find a 12V datasheet)

Starting with the 28BYJ-48 12V DC unipolar stepper motor, http://www.adafruit.com/products/918, I measured the resistance of the pins to determine which is the common pin, to double-check the datasheet, and to practice finding the interface to a stepper motor that has no datasheet.

28BYJ-48 12V | Blue | Pink | Yellow | Orange | Red
Blue | - | 161 ohm | 160 | 162 | 80
Pink | | - | 160 | 161 | 81
Yellow | | | - | 160 | 80
Orange | | | | - | 81
Red | | | | | -

In a Unipolar (one-way voltage) stepper motor, 4 pins will have about the same resistance among any pair, and one pin (the common pin) will have about ½ that resistance between it and each of the other pins. Reassuringly, that's what we see here.

So the Red pin is the common pin, just like the datasheet says.

Now let's calculate current: V = I*R, so V/R = I.

It's rated at 12V so 12/80 = 0.15A, or 150mA. Normally 2 pins are energized at a time, so the current is double that, or 300mA.

Our Arduino power supply outputs nominally 9V, so 9/80 = .112A, or 112mA. Double that = 224mA

The Arduino has a regulated 5V supply, so 5/80 = .062A or 62mA. Double that = 124mA.

Note: online discussions suggest the max 5V Arduino current will be under 500mA, so we probably want to power from the 9V Vin instead of the regulated 5V.

Summarizing the 28BYJ-48 12V

Voltage | Current
12V | 300mA
9V | 224mA
5V | 124mA

Order of pin activation: The datasheet doesn't actually say, but we can quickly and harmlessly experiment with the order. 4 pins taken in any order would produce 4 factorial (4!), which is 4 * 3 * 2 * 1. Fortunately, because the pins run in a cycle, we can pick any one pin and start the cycle with that one. That leaves only 3! combinations, or 3 * 2 * 1 = 6 combinations. Testing a combination is just a matter of initializing the Stepper object in the Sketch with that combination. One of the 6 sequences should produce strong clockwise motion, the reverse of that sequence should produce strong counter-clockwise (anticlockwise) motion, and the other four should produce weak motion if any motion at all. You can test strong vs. weak by holding the turning wheel back a bit to feel how much it resists. Also a good step sequence should be quieter than the bad ones.

Oops! Before testing rotation, I need to put in the steps per revolution and the speed in RPMs – running the motor too fast will make it not rotate properly. Set it to the Adafruit recommendation of 513 steps per revolution and 5 RPMs.

The results:

Stepper stepper(STEPS_PER_REVOLUTION,

//PIN_STEP_BLUE, PIN_STEP_YELLOW, PIN_STEP_PINK, PIN_STEP_ORANGE); // weak clockwise, noisy

//PIN_STEP_BLUE, PIN_STEP_YELLOW, PIN_STEP_ORANGE, PIN_STEP_PINK); // weak clockwise, noisy

PIN_STEP_BLUE, PIN_STEP_PINK, PIN_STEP_YELLOW, PIN_STEP_ORANGE); // strong clockwise, quiet

//PIN_STEP_BLUE, PIN_STEP_PINK, PIN_STEP_ORANGE, PIN_STEP_YELLOW); // strong counterclockwise

//PIN_STEP_BLUE, PIN_STEP_ORANGE, PIN_STEP_YELLOW, PIN_STEP_PINK); // weak CCW, noisy

//PIN_STEP_BLUE, PIN_STEP_ORANGE, PIN_STEP_PINK, PIN_STEP_YELLOW); // weak CCW, noisy

So blue, pink, yellow, orange is the winner. Remember that the Stepper library energizes pins in a different order than the order of pins in the Stepper() constructor here.

I noticed the motor getting a lot warmer than the old, obsolete one did. For comparison, my obsolete motor has a common-to-pin resistance of 193 ohms. At 9V the current is 9/193 = 46mA; double that = 92mA. In contrast, this motor at 9V consumes 224mA = about 2.5 times more current than my old motor.

## October 24, 2015 – Sent Wheel to Ponoko; photo-interrupter

Created another lunar wheel, with just 8 disks – not a lot of lunar images, but a good size. Maybe I'll explore doing one of 10 images sometime.

I added the crescent moon edges, to guide painting. Decided to show crescents and gibbous moons that are ½ way between the quarters, half, and new moons. Calculated the visible fraction at that point: r * cos(45 degrees). Added an outline of our dog, to use as a model for the dog I want in the image.

A while back I read a Ponoko blog on “Scale Fail” http://blog.ponoko.com/2009/08/19/avoid-scale-fail-with-free-prototyping/. It's all about taking advantage of cheap prototypes before committing to a spendy print. Proto 1 = paper (print it to scale on your home paper printer); Proto 2 = cardboard: cardboard is cheap and can be cut using the pattern; Proto 3 is the real thing.'

Printing in paper, I found I'd reversed a couple of the lunar images – that would have wasted one purchase of an MDF cut from Ponoko.

The Sparkfun opto-interrupter and breakout board has arrived, and I soldered it up. With very little difficulty I got it working great. Decided to avoid noise at the edges of the slot by insisting on first seeing a few steps with the opto-interrupter reporting darkness, then searching for the first occurrence of light. That way if the Sketch starts with the wheel at the start of the slot or in the middle of the slot, it should find the start of the slot easily.

## October 23, 2015 – first Ponoko quote

I'm so excited! I learned how to draw horizontal, vertical, etc., lines in Inkscape. I was using the wrong tool; the one I need is the pen (“draw Bezier curves and straight lines”) with the control key held down to constrain the line to angles that are multiples of 15 degrees.

With that new-found knowledge and a bit of time, I created an Inkscape file that had 12 lunar disks and a slot for the photo-interrupter. I successfully uploaded it to Ponoko and got a quote for that design on 1/8”, 15” square MDF: $14 – not a bad start.

On printing out the design and looking at it a bit, I've decided that 12 lunar disks on one wheel results in disks that are too small.

## October 20, 2015 – Exploring laser cutting

Signed up for https://www.ponoko.com/ and read up on what sorts of laser cutting they offer. Thought I'd start out with 1/8” (0.125”) MDF in a 15”x15” piece. Downloaded their Inkscape templates for MDF.

Downloaded Inkscape (https://inkscape.org/) as the Open Source tool I plan to use to create the Laser Cutting diagrams.

Hole placement for the lunar disk: The 5mm-bore set screw hub I'm using has holes 0.5445” apart horizontally or vertically. Further, the screw clearances page, http://www.phy.mtu.edu/~suits/misc/tapsizes.html, lists a “free fit” hole for a 6-32 screw as being 0.1495” in diameter. So I think I want to place the 4 holes at 0.272” (0.5445” / 2) from center in x and y, and 0.1495” diameter. The center of a 15.1” square sheet is 7.550”, 7.550”. Inkscape works in 1,000ths of an inch, so I think the 4 holes should be:

0.149” in diameter, centered at

7.278, 7.278

7.278, 7.822

7.822, 7.822

7.822, 7.278

After a bit of stumbling around in Inkscape (I've never used it before) I created 4 holes which I think are at the right locations and size, and the proper color to indicate cuts (vs. engraving). I next tried to add a cross (two intersecting lines) at the center, and was completely stumped. Drawing a horizontal line in Inkscape seems tricky.

## October 18, 2015 – stepper experiments; ordered new parts

Created the bill of materials. About $140 so far.

In writing the Bill of Materials, I found the stepper motor I'm currently using, an old Jameco 30BYJ02AH unipolar stepper motor, is no longer carried by Jameco (or anyone else I can find).

In looking for a replacement for the no-longer-carried stepper motor, remembered that there's a Stepper arduino library. Put in code to use that instead of the hand-written code I had been using. Also found 2 AdaFruit stepper motors that look promising.

Experimented a lot with the Arduino Stepper library. It does full steps instead of the half-steps specified by my current (obsolete) stepper. After much experimentation and calculation from the stepper motor datasheet, came up with the right settings to run the motor from the Stepper library.

Note: with full steps the motor is fairly weak. I'm concerned that with a large disk of wood attached to it, it may slip. That's something to test with the new stepper motor(s).

Started looking at the datasheet for the opto-interrupter I have. It's too narrow for my use (5mm), but is likely similar to what I'll need.

Ordered 2 types of stepper motors from AdaFruit; ordered a 10mm opto-interrupter from Sparkfun, along with the Sparkfun breakout board for it.

Built the start of the state machine that will run the real Lunar Clock – whee!

## October 16, 2015 – Found a couple non-soldered pins

Decided to check the Transmogrishield + CC3000 Shield combination for wiring continuity.

Mega MOSI → Shield 11 ok

Mega MISO → Shield 12 NOT CONNECTED

Mega SCLK → Shield 13 ok

of the other pins... D10 → D10 NOT CONNECTED

Checking the Transmogrishield alone, both flaws appear on that board.

Checking the CC3000 Shield alone, neither flaw appears on the shield.

So the Transmogrishield has two Not Connected pins that should be connected.

Looking closely, it looks like the top connector joints for D10 and MISO (12) are not connected.

Resoldered those two connections. Now the Mega+Transmogri+CC3000 passed the CC3000 board test, connection test, and WebClient Sketches – it works!

Rewrote LunarClock to use the CC3000 rather than the ESP8266 wifi shield – works great.

## October 15, 2015 – Back to CC3000

Tried many times to get the ESP8266 wifi shield to connect to my wifi hotspot, with no success at all. Played with insulating the USB A connector, replaced the serial comm wires, reseated the board, all to no effect.

Decided to try to get the CC3000 to work again. When it failed last, I was using a seriously out of date Arduino IDE – maybe things will be better now.

Replaced the ESP8266 on the Mega with a Sparkfun Transmogriboard and CC3000. From my notes, this should work out of the box with no software or hardware changes. Yet board test hangs in the board init.

Decided to wipe the CC3000 library and download it afresh. No luck: the board test still hangs, with or without the Transmogrishield.

Tried the CC3000 board test Sketch with the board on an Uno. Works great. Odd.

## October 14, 2015 – Modded LunarClock to use EEPROM

Changed LunarClock code to get WiFi SSID and Password from EEPROM. Committed that change.

Noticed that the WiFi is VERY unreliable for me. Successfully reads about once every 5 times. The rest of the time it either doesn't init the board properly or doesn't successfully query the site. Finally it totally locked up. Mighty frustrating. I wonder whether it's an electrical problem.

### October 13, 2015 – Added an example

Added a simple example to show how to read EEPROM strings written by write_eeprom_strings.

### October 12, 2015 – Committed write_eeprom_strings

Finished cleaning up write_eeprom_strings. Created a github repo for it.

### October 11, 2015 – Wrote write_eeprom_strings

Thinking about how easy it would be to accidentally commit my WiFi credentials into the source, I wote an Arduino Sketch, write_eeprom_strings, that writes the user-entered WiFi SSID and Password into EEPROM. That way, the Sketch can read the WiFi credentials from EEPROM rather than hard-coding them in the Sketch source code.

### August 27, 2015 – Committing the code on GitHub

I moved the library code into a library, then created a GitHub repo for the Sketch (https://github.com/bneedhamia/LunarClock) and another for the library (pointed to by the Sketch code), and committed the code.

### August 25, 2015 – successfully reading the age of the moon

Found the simple bug that was causing a reset: an infinite loop that copied data.

Added code to read and parse the age of the moon (days since the new moon) and illuminated percentage of the face of the moon. Example output:

Reset.

Starting...

Connecting to needhamia4 ...

Connected as 192.168.0.36

Querying astro.ukho.gov.uk ...

Found Date:

days since Sunday: 3

day of month: 26

Month: 8

Year: 2015

Hour: 4

Minute: 2

Second: 20

Days since new moon: 11.30

Percent illuminated: 81

Query completed.

### August 23, 2015 – writing a library to read from ESP8266

Recasting the code into a library to be used in the Lunar Clock. Modifying Lunar Clock to use it instead of the CC3000 WiFi shield.

Everything going well until I added the parsing of the date header:

Reset.

start

Connected as 192.168.0.36

Searching for: Date:

Reset.

start

Connected as 128.0.0.0

Searching for: Date:

It starts searching for the date, then resets.

### August 20, 2015 – Hacked the recognition of closed HTTP session

Strangely, the 0,CLOSED doesn't seem to be preceded by a \n or a \n with any surrounding of \r, yet the output of the 0,CLOSED always begins at the left column. I wonder whether there's a non-printable character in there.

As a hack, I changed the code to recognized the string “0,CLOSED” anywhere in the text. It seems to work fine that way.

### August 18, 2015 – working on reading the moon phase page

I finished adding code to skip the \n+IPD,...: messages from the ESP8266, and the \n0,CLOSED message at the end of the data. That code seemed to work fine on data received from example.com

I then changed the code to read from the real moon phase site, http://astro.ukho.gov.uk/nao/miscellanea/birs2.html.

Unfortunately, the data the ESP8266 returns from that site includes more intrusive characters: frequent insertion of a line consisting of nothing more than a hexidecimal number.

Could it be this is some overrun message, because it takes so long to print the text received from the site? No: upping the serial output speed to 115200 shows the same intruding characters, with the same values. I wonder if the site has some unprintable characters in it?

I now see that the header says “Transfer-Encoding: chunked”, which means there's a further layer of packeting the data. See https://en.wikipedia.org/wiki/Chunked_transfer_encoding for the encoding.

Found that if I specify HTTP 1.0 rather than 1.1 in the header, the site returns data without chunked encoding – no intrusive characters.

Noticed that I still see the 0,CLOSED command at the end, which suggests that the detection of that command is failing. Started debugging that problem. It doesn't seem to find the \n0 sequence. Skipping \r didn't help. So I wonder if there's an unprintable character before the 0.

### August 16, 2015 – Got ESP8266 board working on Arduino Mega

I modified the Sparkfun ESP8266 library to support the Mega Serial1, Serial2, and Serial3.

I modified the Shield Demo to specify Serial3.

I connected shield pin 8 to Mega pin 15 and shield pin 9 to Mega pin 14.

On the shield, I cut the header pins for pin 8 and 9, because leaving them connected to Mega pins 8 and 9 and leaving pins 8 and 9 as default inputs seemed to prevent communication (although I'd expect that leaving those Mega pins as inputs without pullup resistors shouldn't affect the signal. Odd.)

At that point, the demo successfully connected to my WiFi hotspot, but it wouldn't read from www.example.com.

Looking at the demo code, I saw it expects the server to immediately respond, and to keep feeding the board so that client.available() is never false. I wrapped the client.available test in a timeout loop that sleeps 5ms every time client.available() is false – that seemed to do the trick. A longer delay caused the board to lose characters. 1ms would probably be best.

Now the demo program receives all the text from the server, but also (undesireably) echos the communication with the board during reception. See the following example output – note the +IP...: text that intrudes on the output twice, and the final 0,CLOSED.

+IPD,0,1460:HTTP/1.1 200 OK

Accept-Ranges: bytes

…

<p>This domain is established to be used for illustrative examples in documents. You may use this

domain in examples without pri

+IPD,0,150:or coordination or asking for permission.</p>

<p><a href="http://www.iana.org/domains/example">More information...</a></p>

</div>

</body>

</html>

0,CLOSED

Examining the code and the ESP8266 AT-command document, it turns out client.read() maps straight to Serial3.read(), but on receiving data the shield will prefix the data block with +IPD,0,len...: and on closing will send 0,CLOSED

I heavily modified the demo to add a state machine that recognizes and skips “\n+IPD,0”.*”:”

Output looks good:

HTTP/1.1 200 OK

Accept-Ranges: bytes

Cache-Control: max-age=604800

Content-Type: text/html

Date: Mon, 17 Aug 2015 00:04:11 GMT

Etag: "359670651"

Expires: Mon, 24 Aug 2015 00:04:11 GMT

Last-Modified: Fri, 09 Aug 2013 23:54:35 GMT

Server: ECS (rhv/818F)

X-Cache: HIT

x-ec-custom-error: 1

Content-Length: 1270

Connection: close

<!doctype html>

<html>

<head>

<title>Example Domain</title>

<meta charset="utf-8" />

<meta http-equiv="Content-type" content="text/html; charset=utf-8" />

<meta name="viewport" content="width=device-width, initial-scale=1" />

<style type="text/css">

body {

background-color: #f0f0f2;

margin: 0;

padding: 0;

font-family: "Open Sans", "Helvetica Neue", Helvetica, Arial, sans-serif;

}

div {

width: 600px;

margin: 5em auto;

padding: 50px;

background-color: #fff;

border-radius: 1em;

}

a:link, a:visited {

color: #38488f;

text-decoration: none;

}

@media (max-width: 700px) {

body {

background-color: #fff;

}

div {

width: auto;

margin: 0 auto;

border-radius: 0;

padding: 1em;

}

}

</style>

</head>

<body>

<div>

<h1>Example Domain</h1>

<p>This domain is established to be used for illustrative examples in documents. You may use this

domain in examples without pri or coordination or asking for permission.</p>

<p><a href="http://www.iana.org/domains/example">More information...</a></p>

</div>

</body>

</html>

0,CLOSED TIMEOUT

(The TIMEOUT at the end is just a placeholder debug printout).

Next steps: modify the state machine so it also recognizes “\n0,CLOSED” and takes appropriate action.

Note: client.isConnected() can send a string to the board, so I don't want to use that call because it might perturb the state of the board.

The URL of the British site is: HM Nautical Almanac Office: Miscellanea, Daily Rise/set and Twilight times for the British Isles

http://astro.ukho.gov.uk/nao/miscellanea/birs2.html

Important text fragment from that page:

<br>The age of the Moon is 3.3 days old and the illuminated fraction is 10 per cent.

### August 9, 2015 – got Sparkfun ESP8266 wifi shield working on Uno

Uninstalled Arduino; installed from arduino.cc, 64-bit 1.6.5. To install from Arduino.cc on Ubuntu:

1. Install prerequisites (which installing some other Arduino version will do)
2. Download
3. Unpack
4. Move the unpacked folder to home (~)
5. from a terminal, cd to the unpacked arduino folder, sh -x install.sh
6. copy your old sketchbook contents (including libraries) to the newly-created ~/Arduino folder.
7. On the desktop, right-click on the desktop Arduino file and select Properties
8. Click the Permissions tab
9. Check the box marked Allow executing file as program
10. click OK
11. The desktop file should now show the Arduino IDE icon
12. Drag that desktop icon to the execution bar, so you can start Arduino by clicking on that icon in the execution bar..

Installing the latest Arduino IDE (1.6.5) took care of all of the compilation and library-recognition issues I'd had with the old Arduino IDE.

Did a git clone of the Sparkfun ESP8266 library source into the arduino/libraries folder.

Successfully compiled and ran the board demo. Sometimes it wouldn't work – I suspect like the other wifi shield it doesn't fully initialize the chip state on reset (vs. power cycle). Once it successfully connected, it seemed to connect correctly more often.

To run the demo, I had to set the serial monitor to a newline line ending. When the demo asks for input, click Send.

Tried the shield on an Arduino Mega: no luck.

Looked at the schematic. The interface to the Arduino is extremely simple: serial I/O on pins 8 & 9.

http://electronics.stackexchange.com/questions/59259/softwareserial-on-arduino-mega explains that Arduino Mega doesn't support serial I/O on pins 8 and 9:

“In Arduino version 1 and above, SoftSerial was replaced with NewSoftSerial (http://arduiniana.org/libraries/newsoftserial/). This uses interrupts and timers, and is far more efficient. This limits the pins that it can work on though to ones that have pin change interrupts.”

Mega supports software serial on pins 10, 11, 12, 13, 50, 51, 52, 53, 62, 63, 64, 65, 66, 67, 68, 69. Note that pins 8 and 9 are not in that list, which is why the ESP8266 Shield doesn't work with Arduino Mega out of the box.

Note: Mega has 4 hardware Uarts: They are on pins 0/1, 14/15, 16/17, 18/19. So one solution would be to wire the ESP8266 serial I/O pins to pins 14/15, 16/17, or 18/19. (cutting the pins for 8 & 9, making it not work with Arduino Uno any more.)

Alternatively, you could cut the 8/9 header pins on the shield, rewire them to pins 10/11, and of course in both cases mod the library to use the right pins. I think this still wouldn't work on Uno, because 10, 11, 12 are used for I2C.

So it sounds like you can make the board either work on Mega or Uno, but not both.

Seems like a simple thing is to:

- on the shield, cut the legs for the standoffs for pins 8 & 9, so that they don't connect to pins 8 & 9 on the Mega.

- on the shield, use hookup wire to connect pins 8 & 9 of the headers to pins 10 & 11 (find which to connect to which).

- hack the ESP8266 library to use pins 10 & 11 for the software serial.

### August 5, 2015 – Tried the Sparkfun ESP8266 wifi shield

In the meantime, I noticed Sparkfun offers a $15, AT-command-driven Wifi Shield, that seems to support TCP and UDP (vs. just TCP), and sounds simpler than the CC3000 interface. So I bought one, soldered the headers on it, and tried out the main demo example on an Arduino Uno.

Problems:

1. The git repo of the library isn't setup for the version of Arduino IDE I have. I had to copy everything from the src folder to the main folder of the library in order to have the demo app find the header files.
2. The F() macro causes a compiler error. Avoided it by #define F(x) x
3. When the board was pressed tight against the Arduino, the comm with the board failed. Pulling the board out a touch seemed to fix that problem.
4. The board successfully connected to my Wifi hotspot, but printed garbage for the contents of http://example.com. I suspect the problem is that it's running out of data space because I turned off the F() macro.

Next steps:

- Install the latest Arduino IDE. The Ubuntu default version is 1.0.5+..., which is pretty old.

- Find a fix for the F() problem. A quick Google turned up a couple promising notes.

### July 26, 2015 – client.find() fails (accidentally down-rev'ed Arduino IDE)

I've upgraded to Ubuntu 14.04 and probably upped the version of Arduino IDE. [Later I found I downgraded instead of upgraded the version of Arduino IDE.]

I also downloaded a new version of the Sparkfun CC3000 library, so everything is different.

Now client.find() fails: if (!client.find((char *)"Date: ")) { is true.

Yet if I simply do a for loop printing each received character, I see the Date: string.

Odd.

Next: look at the documentation for find() to see what's wrong.

### May 3, 2015 – found a better lunar phase link (but not really)

Somebody pointed out to me that % illumination is ambiguous: that a given illumination happens twice in a lunar month. The moon could be waxing or waning.

Today I found a much better source of the phase of the moon [udpate: that didn’t turn out]: the Apparent Disk of Solar System Object US Naval Observatory page (http://aa.usno.navy.mil/data/docs/diskmap.php). The inputs on that page are:

Object: Moon UT1 Year, Month (1 = Jan), Day, Hour, Minute

Here's an example query: http://aa.usno.navy.mil/imagery/disk?body=moon&year=2015&month=5&day=4&hour=00&minute=22 (http://aa.usno.navy.mil/imagery/disk?body=moon&year=2015&month=5&day=4&hour=00&minute=22)

Example output, somewhat parsed:

Reset.

Connected.

date: 2015-5-4 3:6

30 GMT

Server: Apache

X-UA-Compatible: IE=edge

Connection: close

Transfer-Encoding: chunked

Content-Type: text/html; charset=utf-8

45c

<!doctype html>

<html>

<head>

<title>Apparent disk of the Moon</title>

<link rel="stylesheet" type="text/css" href="/css/imagery-viewer.css"/>

<style type="text/css">

#view { background-image:url('http://api.usno.navy.mil/imagery/moon.png?date=1/1/2015&time=0:00') }

</style>

</head>

<body link="#FFFF00" vlink="#FFFF00" alink="#FFFF00">

<div id="wait"></div>

<div id="view">

<div id="head">

<h1>U.S. Naval Observatory</h1>

<h2>Astronomical Applications Department</h2>

<h3>Apparent disk of the Moon on January 1, 2015 0:00 UT</h3>

</br>

<h2>(Mosaic map courtesy of <a href="http://pdsmaps.wr.usgs.gov/maps.html" target="blank">USGS Astrogeology Science Center</a>)</h2>

</div>

<img class="alt" src="http://api.usno.navy.mil/imagery/moon.png?date=1/1/2015&time=0:00" width="1024" height="1024" alt="Apparent disk of the Moon on January 1, 2015 0:00 UT"/>

<div id="info">

<ul>

<li>Sub-Earth: Lat 3.8&#176;, Lon 5.3&#176;</li>

<li>Sub-solar: Lat 1.5&#176;, Lon 54.9&#176;</li>

<li>Phase: 0.824</li>

<li>Diameter: 31' 8.5"</li>

</ul>

</div>

</div>

</body>

</html>

0

END

Heck. Found the value on this page isn't the age of the moon; it's the % illuminated (0..100..0).

So I still need to find a good page on the age of the moon.

After digging around a lot I found another (British) government site that provides, among other things, the age of the moon (days since the New Moon). That should do the trick (the url is listed later, and in this document's Summary).

### April 26, 2015 – query works, date parsing works with CC3000 and Uno

I bought a Sparkfun CC3000 WiFi Shield and tried it out on an Arduino Uno.

Having a lot of trouble, running out of data memory just trying to initialize the Wifi. Turns out the SD library and my SD Config library take a lot of heap on an Uno. After removing both my library and the SD library, the wifi seems to work. Note that the response contains the required Date header, which will tell us the current date and time.

Reset.

Connecting...

Connected.

HTTP/1.1 200 OK

Date: Mon, 27 Apr 2015 01:15:42 GMT

Server: Apache

Connection: close

Transfer-Encoding: chunked

Content-Type: text/html; charset=UTF-8

146

<!DOCTYPE HTML PUBLIC "-//W3C//DTD HTML 4.01 Transitional//EN" "http://www.w3.org/TR/html4/loose.dtd">

<html>

<head>

<title>Fraction of Moon Illuminated</title>

<meta http-equiv="Content-Type" content="text/html; charset=ISO-8859-1">

<meta name = viewport content='width=device-width, initial-scale=1'>

</head>

<body>

<pre>

10a0

Fraction of the Moon Illuminated, 2015 Astron. Applications Dept.

at Noon U. S. Naval Observatory

Mountain Standard Time Washington, DC 20392-5420

Day Jan. Feb. Mar. Apr. May June July Aug. Sep. Oct. Nov. Dec.

01 0.88 0.95 0.86 0.93 0.95 0.99 1.00 0.97 0.87 0.81 0.67 0.65

02 0.94 0.99 0.92 0.97 0.98 1.00 0.99 0.92 0.78 0.72 0.57 0.55

…

28 0.67 0.79 0.64 0.76 0.78 0.88 0.91 0.98 0.99 0.97 0.90 0.88

29 0.76 0.73 0.83 0.85 0.94 0.96 1.00 0.96 0.92 0.82 0.81

30 0.84 0.81 0.90 0.91 0.98 0.99 0.98 0.90 0.85 0.74 0.72

31 0.91 0.88 0.96 1.00 0.94 0.77 0.64

55

</pre>

<p><a href="javascript:history.go(-1)">Back to form</a></p>

</body>

</html>

0

Got the date parsing working. It now parses the “Date:” header in the response to find out what the current year, month, and day are. Example debug output of the parsed date (gmt): Apr-27-2015

Next steps: decide how to represent the time so the app can decide when to perform the lunar query.

### April 11, 2015:

http://playground.arduino.cc//Code/Webclient is an example of getting the time from any web server's response header fields. The NTP example didn't work for me because the CC3000 supports only TCP (not even UDP).

As for paints: Acrylic paints may be what I'm looking for: bright and non-toxic, and so are used for painting childrens' toys.

Example query: http://aa.usno.navy.mil/imagery/disk?body=moon&year=2015&month=5&day=4&hour=00&minute=22 (date and time are in UTC).

### March 28, 2015: Considering a linear design

The orange-slice model seems complex: the mechanics of either moving the slices in/out of the model or turning each slice over to go black and white looks pretty tricky.

Played around with the idea of a set of discrete images of the moon and a mechanism to either move the proper lunar image into place or move the viewing place over the proper lunar image.

After a few iterations I came up with the idea of a horizontal line of lunar images, and a white cloud or cloud set that has a hole in the middle of it to show the moon. Once every couple days, the cloud slides to the next lunar image.

16 images means one every ~2 days.

For the linear drive of the clouds across the lunar images, think about a gearhead, with a spool on the end that has metal wire wrapped around it. Alternatives: stepper motor that turns a long screw that has bushings on it that ride as the screw turns. Another alternative: stepper motor that turns a timing belt drive that the clouds ride on (that last one is a very common solution).

### February 20, 2015: Made a pattern for a divided lunar disk

Used Geometer's Sketchpad (a program I love) to construct a disk divided into 8 orange-slices.

### January 31, 2015: Hunting for phase of the moon, current time

My idea is to have a craft-wood clock-like thing that shows something like:

- Phase of the moon
- Weather (overcast, clear)

I've also thought about a sort of Prague Astronomical Clock or Astrolabe clock.

I dug a lot for a web site that provides current phase of the moon – not much luck. Found a lot of lunar web sites that are free, but non-sourced (no idea whether they're accurate). Found only the web page from the usno and a couple of books of formulae.

http://aa.usno.navy.mil/rstt/onedaytable?year=2015&month=1&day=31&state=OR&place=North+Plains provides a text listing including "Phase of the Moon on January 31, 2015: Waxing Gibbous with 89% of the Moon's visible disk illuminated." http://aa.usno.navy.mil/data/docs/RS_OneDay.php is the form fillout page for that. Note: that page is odd. Sometimes it seems to give the percent illumination, and other times not.

http://www.usno.navy.mil/USNO/astronomical-applications/software-products provides C code for various astronomical calculations.

http://www.fourmilab.ch/moontoolw/ Moontool for Windows is an old, old public domain program.

http://www.fourmilab.ch/homeplanet/ obsoletes Moontool. Also public domain.

Those calculate based on

http://www.amazon.com/exec/obidos/ASIN/0943396611/fourmilabwwwfour

http://www.programmableweb.com/category/all/apis?keyword=moon turns up 7 apis, none of which seem authoritative or government based.

I think either usno or the books are my best bet.

http://stardate.org/nightsky/moon gives a calendar of the moon, which is useful for designing how many phases the design will support.

http://aa.usno.navy.mil/data/docs/MoonFraction.php provides the percent of the moon that's illuminated in a given time zone for the year, but percent is ambiguous: a given percentage happens twice per month (waxing and waning).

Need to do a call to get the current time, so the lunar clock moves at the same time of the day.

http://playground.arduino.cc/Code/NTPclient is an Arduino NTP client that seems easy and small.

Think about the physical form: a wooden model of the moon's phase – of some sort.

One idea: cut a flat disk along longitude lines, evenly spaced horizontally. Color each slice deep blue on one side, moon-surface-colored on the other. To remove a slice from the lighted moon, rotate it 180 degrees in the X axis. Sounds like it would look cool.

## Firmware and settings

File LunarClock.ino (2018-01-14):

/*
   Net-connected lunar clock.
   Rotates a dial showing the current phase of the moon,
   as reported by HM Nautical Almanac Office: Miscellanea,
   Daily Rise/set and Twilight times for the British Isles,
   at http://astro.ukho.gov.uk/nao/miscellanea/birs2.html

   Note: that web page is Crown Copyright.
   Read the site Copyright and Licensing page before using it.

   Copyright (c) 2015, 2017 Bradford Needham
   { @bneedhamia , https://www.needhamia.com }

   Licensed under GPL V2
   a copy of which should have been supplied with this file.
*/
//345678901234567890123456789312345678941234567895123456789612345678971234567898

/*
   This sketch requires a Sparkfun ESP8266 Thing Dev board
   (https://www.sparkfun.com/products/13804),
   a 28BYJ-48 12V unipolar stepper motor
   (Datasheet at http://www.emartee.com/product/41757/)
   controlled by a set of discrete parts (TIP120s),
   a photo-interrupter for aligning the image of the moon
   (https://www.sparkfun.com/products/9299),
   a level shifter to convert the 5V photo-interrupter output
   into a 3.3V ESP8266 input,
   and several more parts.
   See BillOfMaterials.ods for the complete parts list.

   See the Sparkfun ESP8266 Thing Dev board page above
   for instructions on installing the Arduino ESP8266 support.

   ESP8266 Note: for the WiFi to function properly,
   there must never be a time longer than say 1 second where
   either delay() or loop() is not called.
   That implies that no delay() call can be longer than say 1 second.

   ESP8266 Thing Dev board I/O pin notes:
   - Pin 2 seems unusual. When I connected it to the photo-interrupter output,
     The ESP8266 just kept resetting over and over.
   - Several people caution that Pin 15 must be LOW at boot time,
     or else the ESP8266 will try to boot from an external device.
     I haven't noticed that problem.
*/

#include <float.h>       // For DBL_MAX
#include <ESP8266WiFi.h> // Defines WiFi, the WiFi controller object
#include <ESP8266HTTPClient.h>
#include <EEPROM.h>      // NOTE: ESP8266 EEPROM library differs from Arduino's.

/*
   I/O Pins:

   Pins controlling the stepper motor.
   These pins control the Base voltages of each
   of the 4 non-common wires of the stepper motor.
   The 5th pin (Red) is connected to Vin.

   These pins are Active High.  That is, a HIGH value grounds the
   corresponding wire and coil, energizing that coil.
   PIN_STEP_ORANGE
   PIN_STEP_YELLOW
   PIN_STEP_PINK
   PIN_STEP_BLUE

   PIN_LED_L = LOW to light the yellow LED (and the on-board LED).
     The _L suffix indicates that the pin is Active-Low.
     Active-Low because that's how the ESP8266 Thing Dev board
     on-board LED is wired.

   PIN_LIGHT_DETECTED = input from the photo-interruptor.
     HIGH = the detector is unobstructed (the detector's light is detected).
     That is, part of the lunar wheel's slot is in front
     of the photo-interrupter.
*/

const int PIN_STEP_ORANGE = 12;
const int PIN_STEP_PINK = 13;
const int PIN_STEP_YELLOW = 4;
const int PIN_STEP_BLUE = 0;

const int PIN_LED_L = 5;

const int PIN_LIGHT_DETECTED = 15;

/*
   The EEPROM layout, starting at START_ADDRESS, is:
   WiFi SSID = null-terminated string 0
   WiFi Password = null-terminated string 1
   EEPROM_END_MARK

   To write these values, use the Sketch write_eeprom_strings.
   See https://github.com/bneedhamia/write_eeprom_strings
*/
const int START_ADDRESS = 0;      // The first EEPROM address to read from.
const byte EEPROM_END_MARK = 255; // marks the end of the data we wrote to EEPROM
const int EEPROM_MAX_STRING_LENGTH = 120; // max string length in EEPROM

/*
   States of our state machine that controls what to do inside loop().

   STATE_ERROR = encountered an unrecoverable error. Do nothing more.
   STATE_FINDING_SLOT = turning the wheel to the edge of the slot.
     In this state, stepsRemaining is the number of steps remaining before
     we give up our search for the slot.
   STATE_TURNING_TO_FIRST_IMAGE = turning the wheel to center the first
     lunar image in the display.
     In this state, stepsRemaining is the number of steps remaining to turn
     the wheel before we're done.
   STATE_WEB_QUERY = query the web site to find the time and moon phase.
   STATE_TURNING_TO_IMAGE = turning the wheel to show the correct moon phase.
     In this state, stepsRemaining is the number of steps remaining to turn
     the wheel before we're done.
   STATE_WAITING = waiting for the time to query the site again.
*/
const byte STATE_ERROR                  = 0;
const byte STATE_FINDING_SLOT           = 1;
const byte STATE_TURNING_TO_FIRST_IMAGE = 2;
const byte STATE_WEB_QUERY              = 3;
const byte STATE_TURNING_TO_IMAGE       = 4;
const byte STATE_WAITING                = 5;

/*
   STEPS_PER_REVOLUTION = the number of (integer) steps in one revolution
   of our stepper motor.
   The Adafruit datasheet for the 28BYJ-48 12V motor  at http://www.adafruit.com/products/918
   lists 32 steps per revolution with a further gear ration of 16.025
   which gives 32 * 16.025 = 512.8 steps per revolution.
   Rounding to 513 produces an error of +0.2 steps per revolution
   (that is, one of our revolutions is 0.2 steps larger than the real one).
*/
const int STEPS_PER_REVOLUTION = 513;

/*
   Because there may be noise (uncertainty) as the edge of the slot appears
   in front of the photo-interrupter, we start turning the stepper motor,
   then we expect to see the photo-interrupter dark for
   at least MIN_DARK_STEPS contiguous steps (to get past the end of the slot)
   before we start looking for the slot.

   STEPS_SLOT_TO_MOON = the number of steps between
   the detected start of the slot and the proper alignment of a lunar image
   in the clock's window.
   That is, how much to move after finding the slot.
*/
const int MIN_DARK_STEPS = STEPS_PER_REVOLUTION / (360 / 5); // 5 degrees
const int STEPS_SLOT_TO_MOON = 33; //XXX need to calibrate this when the clock is finished.

/*
   NUM_MOON_IMAGES = the number of lunar images in the wheel.
     We assume the images evenly divide one mean synodic month
     (new moon to new moon), rather than, for example,
     some image being 4 days long while another is 6 days long.
   DAYS_PER_IMAGE = the number of days corresponding to each lunar image.
     29.53059 is the length in days of the mean synodic month.
   STEPS_PER_IMAGE = the number of steps to move from one image to the next.
     Note: we keep current angle and steps per image in floating point
     because NUM_MOON_IMAGES likely doesn't evenly divide STEPS_PER_REVOLUTION,
     which would result in the image alignment drifting significantly
     over a few months.

   INITIAL_IMAGE_ANGLE_STEPS = the number of steps from the center of
     the new moon image to the initial image.
     That is, the initial angle of the wheel relative to the new moon.
*/
const int NUM_MOON_IMAGES = 8;
const double DAYS_PER_IMAGE = 29.53059 / (double) NUM_MOON_IMAGES;
const double STEPS_PER_IMAGE = ((double) STEPS_PER_REVOLUTION) / NUM_MOON_IMAGES;
const double INITIAL_IMAGE_ANGLE_STEPS = STEPS_PER_IMAGE * 5.0;  //XXX need to change this when the mech. design is done.

/*
   Width (milliseconds) of each (half) step in the stepper motor sequence.
   Experimentation shows 4ms is good; 10 is strong & slow; 2 is fast & weak.

   Calculating RPM from PULSE_WIDTH_MS:
   mS/minute   * revolutions/step     * steps/mS = revolutions/minute =
   mS/minute   / steps per revolution / (2 * PULSE_WIDTH_MS) =
   (1000 * 60) / 512.8                / 20 = about 5.8 RPM
   Experimentally, one revolution took about 10 seconds, which would be 6 rpm.
   So this looks right.

   NOTE: During PULSE_WIDTH_MS, the stepper motor is drawing its full current,
   so we want to choose the smallest value of PULSE_WIDTH_MS that turns the disk.
*/
const int PULSE_WIDTH_MS = 10;

/*
 * XXX UNUSED because the current code doesn't read the date/time header field
 * from the web response. Need to learn how to do that with the ESP8266 lib.
   The Date and Time returned from findDate().
   I would have used the C++ struct tm,
   but that didn't seem to be available in the Arduino library.
   NOTE: some fields' values differ from the corresponding fields in struct tm.
*/
struct HttpDateTime {
  short daySinceSunday; // 0..6 Sunday = 0; Monday = 1; Saturday = 6
  short year;           // 1900..2100
  short month;          // 1..12 January = 1
  short day;            // 1..31  Day of the month
  short hour;           // 0..23  Midnight = 0; Noon = 12
  short minute;         // 0..59
  short second;         // 0..61 (usually 0..59)
};

/*
   curentAngleSteps = the current position of the wheel, in (fractional) steps
   from the center of the new moon.

   A floating-point number to avoid accumulating errors
   in dividing a revolution by the number of images,
   which would cause the images to drift out of place
   after a few months of constant running.
*/
double currentAngleSteps;

/*
   28BYJ-48 12V Stepper motor sequence.

   SEQUENCE_STEPS = number of values in sequence[].
   sequence[] = the sequence of pin activation for clockwise rotation
     of the stepper motor.
   curSeq = the index into sequence[] corresponding to the current state
     of the motor. Note: on reset, we don't know the state of the motor,
     but it doesn't matter because we'll rotate the motor to a
     known location (the slot).

   The commented-out sequences are the other 5 possible sequences of the 4 pins.
*/
const int SEQUENCE_STEPS = 4;
const int sequence[SEQUENCE_STEPS] =
{PIN_STEP_BLUE, PIN_STEP_YELLOW, PIN_STEP_PINK, PIN_STEP_ORANGE};    // strong clockwise
//{PIN_STEP_BLUE, PIN_STEP_YELLOW, PIN_STEP_ORANGE, PIN_STEP_PINK};    // quiver (no movement)
//{PIN_STEP_BLUE, PIN_STEP_PINK, PIN_STEP_YELLOW, PIN_STEP_ORANGE};    // quiver
//{PIN_STEP_BLUE, PIN_STEP_PINK, PIN_STEP_ORANGE, PIN_STEP_YELLOW};    // quiver
//{PIN_STEP_BLUE, PIN_STEP_ORANGE, PIN_STEP_YELLOW, PIN_STEP_PINK};    // quiver
//{PIN_STEP_BLUE, PIN_STEP_ORANGE, PIN_STEP_PINK, PIN_STEP_YELLOW};    // strong counterclockwise
int curSeq;

// WiFi Client control object. SAY MORE ABOUT THIS.
HTTPClient httpGet;
WiFiClient *pHttpStream = 0; // stream of data from the Http Get

/*
   The date is received from the Http "Date:" header in the web response we receive.
   Note: that date is GMT rather than local time, but we don't care
   because we use the date/time only to decide when to read the web site again.
*/
struct HttpDateTime dateTimeUTC;

/*
   Moon data from the web site:

   daysSinceNewMoon = number of days (0.0 .. 29.53) since the New Moon.
   illuminatedPC = percent (0..100) of the moon's surface that's illuminated (unused).
*/
double daysSinceNewMoon;
int illuminatedPC;

/*
   The site to query:
     HM Nautical Almanac Office: Miscellanea.
     Daily Rise/set and Twilight times for the British Isles.

   Notes:
   - HTTP 1.0 (rather than 1.1) is specified here to prevent
     the server from using Transfer-encoding: chunked,
     which is difficult to read.
   - "Connection: close" is used to cause the server to
     close the connection when the response is completed.
   - The page takes several seconds to load, because
     the site seems to pause in the middle, and it's a long page.
   - The current age of the moon and % illumination is given
     very near the end of the text of the web page.
*/
//const char HttpServer[] = "astro.ukho.gov.uk";
//const String HttpRequest = "GET /nao/miscellanea/birs2.html HTTP/1.0\n"
//                           "Host: astro.ukho.gov.uk\n"
//                           "Connection: close\n"
//                           "\n";
const char PageUrl[] = "http://astro.ukho.gov.uk/nao/miscellanea/birs2.html";


/*
   The state machine variables.

   state = The current state of the state machine that runs the loop().
     See STATE_* above.
   stepsRemaining = In some states, if non-zero, the number of steps
     remaining to turn the wheel. See STATE_* for details.
   numDarkStepsSeen = In STATE_FINDING_SLOT, the number of continuous
     dark (not in the slot) steps seen so far.
*/
byte state;
int stepsRemaining;
int numDarkStepsSeen;

/*
   WiFi access point parameters.

   wifiSsid = SSID of the network to connect to. Read from EEPROM.
   wifiPassword = Password of the network. Read from EEPROM.
   wifiSecurity = security mode of the network.
   wifiTimeoutMs = timeout (in milliseconds) to wait before deciding
    the connection to the network has failed.
*/
char *wifiSsid;
char *wifiPassword;
//XXX should put the security type in the EEPROM as well.
//unsigned int wifiSecurity = WLAN_SEC_WPA2; // security type of the network.
unsigned int wifiTimeoutMs = 20 * 1000;  // connection timeout.

/*
   Declarations of our functions. See their definitions (code)
   for how they're used.
*/

// Called once automatically on Reset.
void setup() {
  Serial.begin(9600);

  // Set up all our pins.

  pinMode(PIN_LED_L, OUTPUT);
  digitalWrite(PIN_LED_L, HIGH); // ESP8266 Thing Dev LED is Active Low

  pinMode(PIN_LIGHT_DETECTED, INPUT);

  pinMode(PIN_STEP_ORANGE, OUTPUT);
  digitalWrite(PIN_STEP_ORANGE, LOW);
  pinMode(PIN_STEP_PINK, OUTPUT);
  digitalWrite(PIN_STEP_PINK, LOW);
  pinMode(PIN_STEP_YELLOW, OUTPUT);
  digitalWrite(PIN_STEP_YELLOW, LOW);
  pinMode(PIN_STEP_BLUE, OUTPUT);
  digitalWrite(PIN_STEP_BLUE, LOW);

  // Wait a bit for Serial to work properly.
  // Remember we can't delay() for very long without confusing the WiFi.
  for (int i = 0; i < 10; ++i) {
    delay(50);
  }

  Serial.println(F("Reset."));

  state = STATE_ERROR;

  // read the wifi credentials from EEPROM, if they're there.
  wifiSsid = readEEPROMString(START_ADDRESS, 0);
  wifiPassword = readEEPROMString(START_ADDRESS, 1);
  if (wifiSsid == 0 || wifiPassword == 0) {
    Serial.println(F("EEPROM not initialized."));
    state = STATE_ERROR;
    return;
  }

  // Do the one-time WiFi setup:
  WiFi.mode(WIFI_STA);    // Station (Client), not soft AP or dual mode.
  WiFi.setAutoConnect(false); // don't connect until I say
  WiFi.setAutoReconnect(true); // if the connection drops, reconnect.

  connectToAccessPoint(); //What if the access point is down?

  Serial.println(F("Starting."));
  /*
     Initialization is complete.
     Next, we rotate the lunar wheel to a known starting place.
  */
  beginFindingSlot();
}

// Called continuously and automatically.
void loop() {
  int i;

  switch (state) {

    case STATE_ERROR: // unrecoverable error.  Stop.
      // Blink an led
      if ((millis() % 1000) < 500) {
        digitalWrite(PIN_LED_L, HIGH);
      } else {
        digitalWrite(PIN_LED_L, LOW);
      }
      delay(10); // so we don't spend all our time doing digitalWrite()
      break;

    case STATE_FINDING_SLOT:  // rotate the wheel to the slot, so we know the wheel position.
      runStateFindingSlot();
      break;

    case STATE_TURNING_TO_FIRST_IMAGE: // rotate the wheel to the first lunar image.
      if (stepsRemaining > 0) {
        step();
        --stepsRemaining;
      } else {
        // We've finished turning the wheel. Start the web query.
        currentAngleSteps = INITIAL_IMAGE_ANGLE_STEPS;
        state = STATE_WEB_QUERY;
      }
      break;

    case STATE_WEB_QUERY:      // Find the date and the phase of the moon.
      if (!doNetworkWork()) {
        //XXX set how long to wait, say 1 minute.  Keep track of # of fails.
        state = STATE_WAITING;
        break;
      }

      /*
         We now know the date and the phase of the moon.
         Set up the state machine to turn the wheel to the
         correponding image.
      */
      beginTurningToImage();
      break;

    case STATE_TURNING_TO_IMAGE:  // turning the wheel to the current phase of the moon
      if (stepsRemaining > 0) {
        step();
        --stepsRemaining;
      } else {
        // We've finished turning the wheel. Wait until time to query again.
        state = STATE_ERROR; //XXX for now.
      }
      break;

    case STATE_WAITING:   // waiting until it's the right time to query again.
      //XXX this state is used to retry a failed query as well as to wait a day to query again.
      //XXX watch out for daylight saving time.  Just do an offset from midnight UTC,
      //XXX knowing that it will be an hour different in daylight time.
      //XXX be aware that millis() will overflow every ~49.7 days.
      //XXX 24 hours = (unsigned long) 1000 * 60 * 60 * 24 = 86,400,000 milliseconds.
      state = STATE_ERROR; //XXX for now.
      break;

    default:
      Serial.print(F("Unknown state, "));
      Serial.println(((int) state) & 0xFF);
      state = STATE_ERROR;
  }
}

/*
   Begin the process of turning the wheel to find the slot.
   The finding of the slot will be done in STATE_FINDING_SLOT.
*/
void beginFindingSlot() {
  state = STATE_FINDING_SLOT;

  // Turn up to 1 and 1/4 revolutions to find the slot in the wheel.
  stepsRemaining = STEPS_PER_REVOLUTION + (STEPS_PER_REVOLUTION / 4);
  numDarkStepsSeen = 0;

  step();
  --stepsRemaining;
}

/*
   Performs the STATE_FINDING_SLOT loop().
   Called each time the state machine is in the STATE_FINDING_SLOT state.

   Because there can be noise at each edge of the slot,
   the algorithm for finding the slot is:
   1) Turn until we see MIN_DARK_STEPS contiguous steps outside the slot.
   2) Turn until we see the slot.

   There are three outcomes from this function:
   1) Error: we've turned the disk a lot without finding the slot.
   2) Not yet. We haven't yet found the slot.
   3) Yes. We've found the slot.
*/
void runStateFindingSlot() {

  if (numDarkStepsSeen < MIN_DARK_STEPS) {
    // We're still looking to be clearly outside the slot.

    if (digitalRead(PIN_LIGHT_DETECTED) == LOW) {
      // (possibly) outside the slot.
      ++numDarkStepsSeen;
    } else {
      // (still/again) in the slot. Start over.
      numDarkStepsSeen = 0;
    }
  } else {
    // We're clearly outside the slot, looking for the edge of the slot.

    if (digitalRead(PIN_LIGHT_DETECTED) == HIGH) {
      // We have found the slot.  Move to the first image.

      state = STATE_TURNING_TO_FIRST_IMAGE;
      stepsRemaining = STEPS_SLOT_TO_MOON;

      step();
      --stepsRemaining;

      return;
    }
  }

  // We want to turn the disk another step.

  if (stepsRemaining <= 0) {
    // We've turned the wheel as far as we can and have not found the slot.
    state = STATE_ERROR;
    return;
  }
  step();
  --stepsRemaining;
}

/*
   Begin the process of turning the wheel to the lunar image
   that corresponds to daysSinceNewMoon.
   The finding of the slot will be done in STATE_TURNING_TO_IMAGE.
*/
void beginTurningToImage() {
  double desiredAngleSteps;

  state = STATE_TURNING_TO_IMAGE;

  desiredAngleSteps = moonAgeToAngleSteps(daysSinceNewMoon);

  // This calculation isn't quite right.
  stepsRemaining = (int) (desiredAngleSteps - currentAngleSteps + 0.5);
  while (stepsRemaining < 0) {
    stepsRemaining += STEPS_PER_REVOLUTION;
  }

  /*
   * Take the first step.
   * If we're already where we want to be, don't step.
   * STATE_TURNING_TO_IMAGE will take things from here.
   */
  if (stepsRemaining > 0) {
    step();
    --stepsRemaining;
  }

  /*
     Update the position of the wheel relative to the new moon,
     in anticipation of having moving there.
  */
  currentAngleSteps = desiredAngleSteps;
}

/*
   Converts the given age of the moon into the angleSteps
     (see currentAngleSteps) of the corresponding lunar image.
   daysSinceNewMoon = age of the moon, in fractional days since the new moon.

   Returns the fractional angle of the corresponding lunar image,
*/
double moonAgeToAngleSteps(double daysSinceNewMoon) {
  int desiredIndex = 0;  // index of the lunar image to display; new moon = 0.
  double desiredAngleSteps = 0.0; // value to return.

  // Find which image we want to move to (rounded to an integer).
  desiredIndex = (int) ((daysSinceNewMoon + (DAYS_PER_IMAGE / 2)) / DAYS_PER_IMAGE);

  Serial.print(F("Moving to image "));
  Serial.println(desiredIndex);

  // Floating point calculations can produce a slightly over-range value. Fix it.
  if (desiredIndex > NUM_MOON_IMAGES - 1) {
    desiredIndex = NUM_MOON_IMAGES - 1;
  }

  desiredAngleSteps = desiredIndex * STEPS_PER_IMAGE;

  return desiredAngleSteps;
}

/*
 * Connect to the local WiFi Access Point.
 * The Auto Reconnect feature of the ESP8266 should keep us connected.
 */
void connectToAccessPoint() {
  Serial.print(F("Connecting to "));
  Serial.println(wifiSsid);

  WiFi.begin(wifiSsid, wifiPassword);
  // Wait for the connection or timeout. Put this in the state machine.
  int wifiStatus = WiFi.status();
  while (wifiStatus != WL_CONNECTED)
  {
    delay(100);
    Serial.print(".");

    wifiStatus = WiFi.status();
  }

  Serial.println();

  Serial.print(F("Connected, IP address: "));
  Serial.println(WiFi.localIP());

}

/*
   Performs one run of our network activity:
   Connects to the WiFi access point,
   performs the lunar phase query,
   then disconnects.

   Returns true if successful; false otherwise.
*/
boolean doNetworkWork() {
  // Do a query to get the date and the age of the moon.

  if (!query(&dateTimeUTC, &daysSinceNewMoon, &illuminatedPC)) {
    Serial.println(F("Query Failed."));
    httpGet.end();
    // wifi.disconnect(); How to disconnect the ESP8266 WiFi?
    return false;
  }

  httpGet.end();
  // wifi.disconnect();
  return true;
}
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

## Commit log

2015-10-17 replaced the ESP8266 with CC3000
    [LunarClock.ino]
2015-10-19 testing stepper motor; added initial bill of materials
    [BillOfMaterials.ods]
2015-10-19 Runs a stepper motor; state machine for the whole clock is somewhat defined
2015-10-20 added my current project diary, for fun.
2015-10-25 added lunar wheel laser cutting pattern
    [BillOfMaterials.ods]
2015-10-25 added Lunar Wheel laser cutting file
2015-10-25 opto-interrupter is integrated; the wheel-turning part of the state machine is built; awaiting mechanical design
2015-10-27 switched to try out the 12V 28BYJ-48 stepper motor
2015-10-28 switched to stepper 28BYJ-48 12V...sort of
2015-10-29 in the middle of updating for the AdaFruit version of the 28BYJ-48 12V stepper motor
2015-10-29 replacing the obsolete stepper with the AdaFruit 28BYJ-48
2015-10-30 Replaced Stepper library with my own half-stepper code; updated bill of materials
    [BillOfMaterials.ods]
2015-11-02 just notes. Drilled mounting holes into the Sparkfun Photo-interrupter breakout board
2015-11-04 measured a few stepper motors resistances; soldered the hacked photo-interrupter breakout board
2016-01-01 wired and mounted the photo-interrupter
2017-09-01 Update ReadMe to show the stalled state
2017-09-02 Started porting to ESP8266 Thing Dev board
2017-09-02 Reinstalled Arduino to get Esp8266 code to work
2017-09-03 Switching to Sparkfun ESP8266 Thing Dev board. Reads from EEPROM correctly; Blinks LED correctly; doesn't connect to the Access Point yet.
    [LunarClock.ino]
2017-09-03 Successfully reads the moon phase using a Sparkfun ESP8266 Thing Dev board
2017-09-03 Wired and successfully tested the Stepper Motor interface; next step: wiring the photo-interrupter
2017-09-03 Successfully wired the photo-interrupter; learned that there's something odd about pin 2; now net connection fails if the wheel turns before attempting the connection.
    [LunarClock.ino]
2017-09-05 Modified the state machine to find the slot one step per loop. Code has not been tested yet.
2017-09-05 Rewrote the Find The Slot code to do only one step() per loop(). Changed the config of the WiFi. Now seems to rotate to the starting image, then successfully read the web site. So now it's fully port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
2017-09-05 Added a quick note to the diary about the 0 savings caused by replacing the Mega with an ESP8266 Thing Dev board.
2017-09-05 Updated the Bill of Materials to reflect the ESP8266 design. Added a project photo. Did a pass through the ReadMe.
    [BillOfMaterials.ods]
2017-09-05 added a level converter to the BOM
    [BillOfMaterials.ods]
2017-12-04 starting to design 3D printed parts
    [lunarDisk.FCStd]
2017-12-10 Checkpoint on the way toward the 3D printed design
    [CrescentSetup.FCStd, lunarDisk.FCStd]
2017-12-11 Made another shot at the lunar images
    [CrescentSetup.FCStd, lunarDisk.FCStd]
2018-01-10 tweaking the experimental 3D holder for the opto-interrupter
    [clipTest.FCStd]
2018-01-14 Finished clip to hold photo interrupter
    [BillOfMaterials.ods, LunarDisk.stl, StepperHolder.stl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]
